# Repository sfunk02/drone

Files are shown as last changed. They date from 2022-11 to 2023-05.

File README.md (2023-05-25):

# Drone

## by Sam Funk and Paul Schakel

#### [Drone 1.0](https://github.com/sfunk02/drone#drone-10) | [Drone 2.0](https://github.com/sfunk02/drone#drone-20) | [Drone 3.0](https://github.com/sfunk02/drone#drone-30) | [Drone 4.0](https://github.com/sfunk02/drone#drone-40) | [Final Takeaways](https://github.com/sfunk02/drone#final-takeaways)

## Introduction

The goal of this project was to create a drone using a Raspberry Pi Pico. The assignment criteria are as follows:
* Survivability: the payload (RPi Pico, sensors, etc) must survive and function post-flight.
* Custom circuit board: breadboards are for prototyping, not for finished products.  Solder headers onto your board so everything is compact but you can add/remove the Pico and other sensors.
* Data collection: your payload must collect data throughout the flight and save that data to the Pico’s onboard storage. Examples: spin rate (MPU6050), altitude (MPL3115A2), location (GPS).
* Data presentation: Show off that data you collected! Plot the data in some way that is meaningful to your project. 

We decided that a drone would be a reasonably challenging way to accomplish this task.

### Project [Planning](docs/Planning.md)

The initial design was derived from a DJI Tello drone. We wanted the drone to be as compact and small as possible to reduce weight so it could be lifted by our Tello motors. We intend to add cages for the propellers to add a level of safety to the drone, but they were not included in our first prototype. The nature of the project is to make something fly with a Raspberry Pi Pico, so that is the microcontroller we chose to use. We decided to power our prototype with a 2000mAh LiPo battery and two DRV8833 H-bridges because we have a surplus of both in our engineering lab.

### Tools Used

* CAD - [Onshape](https://www.onshape.com/en/)
* Code - [VS Code](https://code.visualstudio.com/)
* Wiring Diagram - [Fritzing](https://fritzing.org/)

### Code Prototypes

To make sure we didn't get ahead of ourselves, we created prototypes of the separate parts of the project so that we could test the components before assembling the whole drone:

* [MPU6050 (accelerometer)](/code/prototypes/accelerometer.py)
* [DRV8833 (old H-bridge)](/code/prototypes/drv8833.py)
* [TB6612FNG (new H-bridge)](/code/prototypes/tb6612fng.py)

<br>
<br>

## Drone 1.0

### Bill of Materials

* Raspberry Pi Pico
* 2000mAh LiPo battery
* x2 DRV8833 (old H-bridge)
* MPU6050 (accelerometer)
* PowerBoost
* acrylic
* ABS (3D print material)
* x4 Tello motors
* x4 Tello propellers
* x4 1.25mm female JST connectors
* circuit board
* wires and solder
* hardware to attach arms and base

### CAD [(Onshape)](https://cvilleschools.onshape.com/documents/ce9d8d739d2d9f15e9173bc0/w/6c76af61bf90a62108bdc466/e/912e9d444323990bdd98e468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)

#### Arm
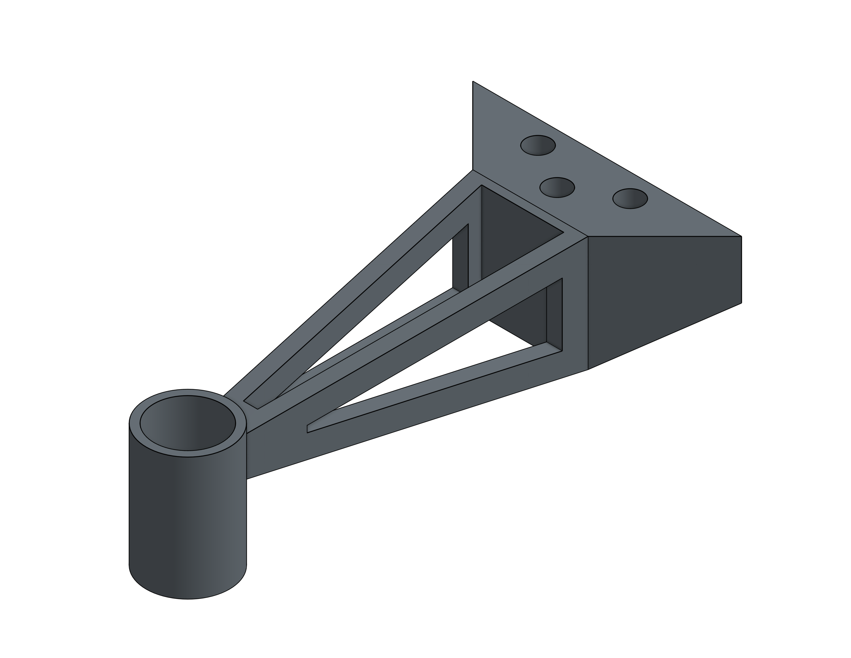
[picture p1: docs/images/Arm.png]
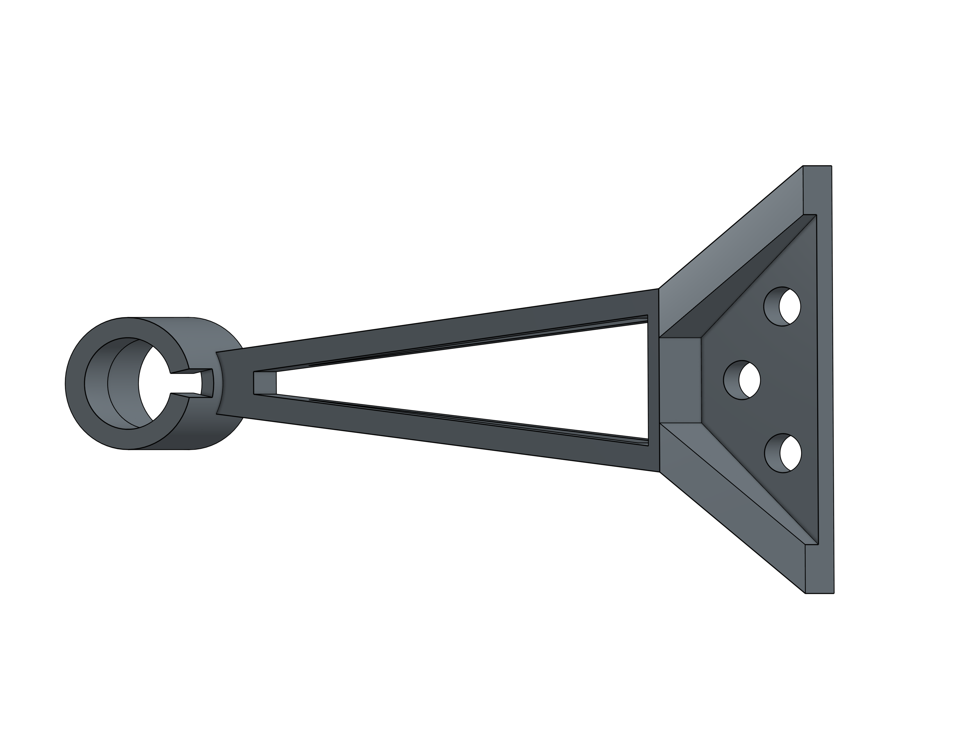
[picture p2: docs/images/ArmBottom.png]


The arm is designed to be lightweight and stable. It accomplishes this with a tapered, hollowed out design. It has a cylinder on the end to fit the motor which acts secondarily as a foot with a small cut-out for wiring to fit through.

#### Base
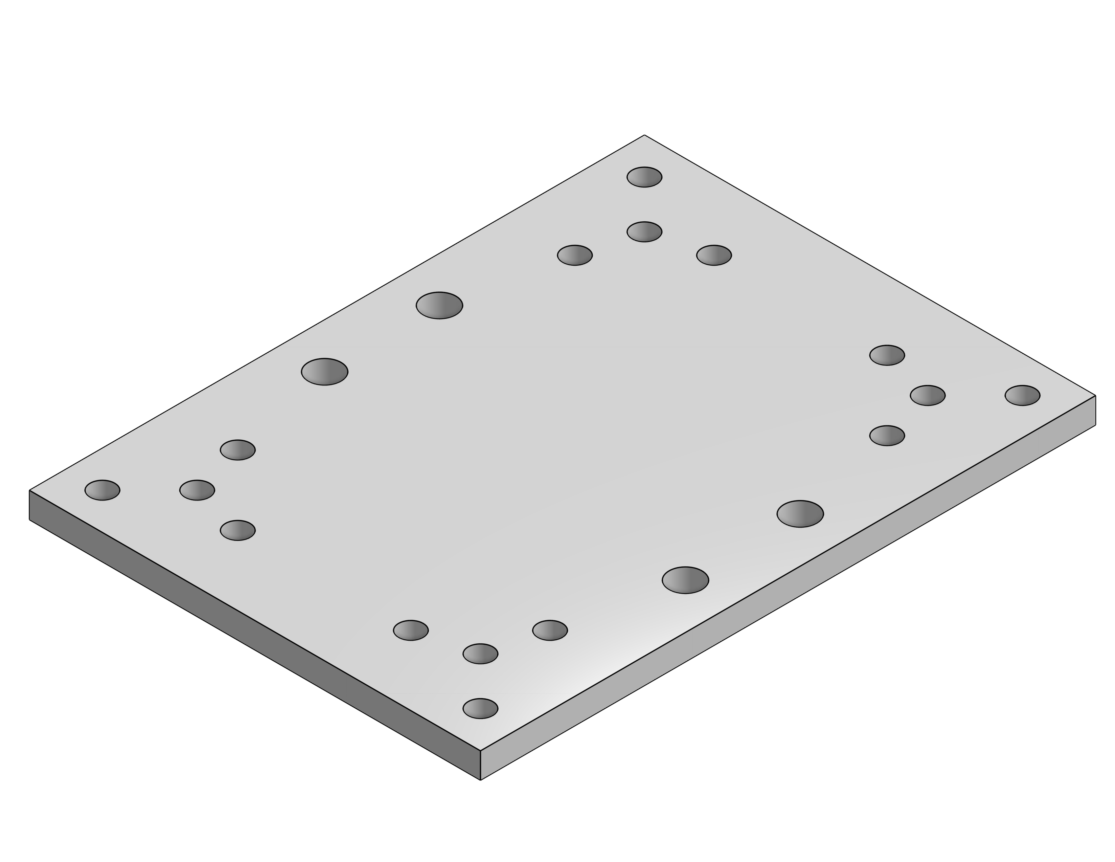
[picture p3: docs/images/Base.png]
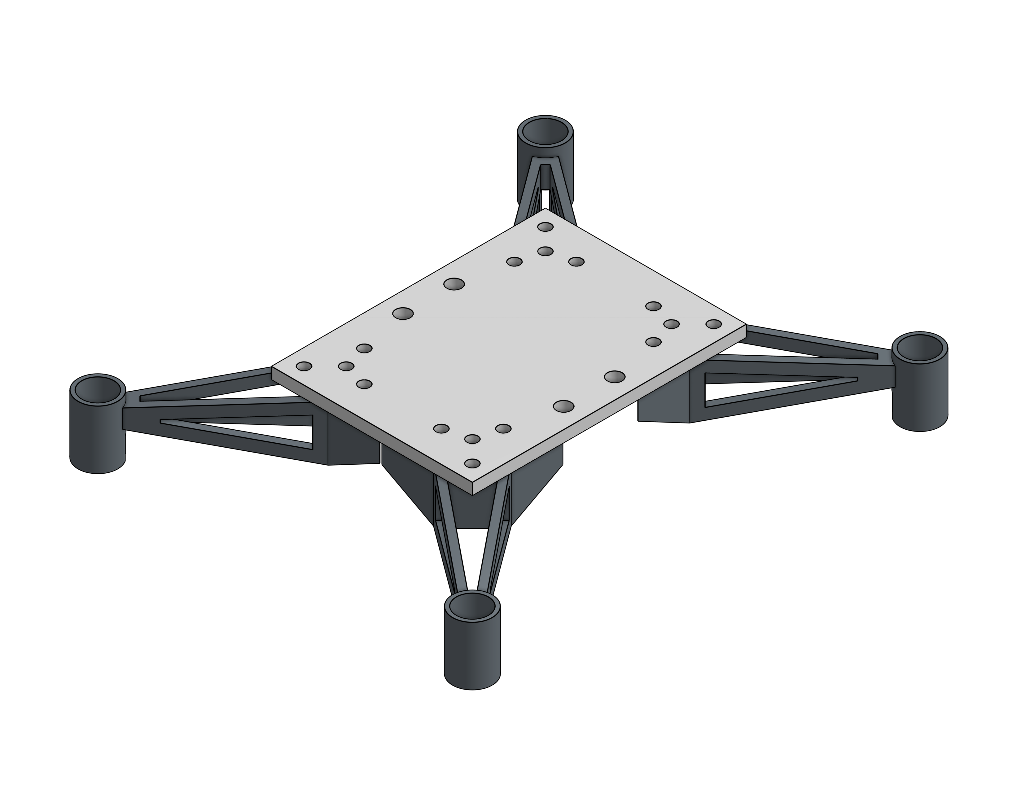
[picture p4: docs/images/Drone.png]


The base is sized to fit our circuit board of components, which includes a Raspberry Pi Pico, two motor h-bridges, an accelerometer/gyro, and a PowerBoost. The CAD assembly allowed me to measure between the arms and make sure there was space to fit the LiPo battery underneath. The four holes in the middle of the base allow the battery to be tied to the drone.

### Code

[Link to Code](code/final_code_1.0.py)

### Wiring

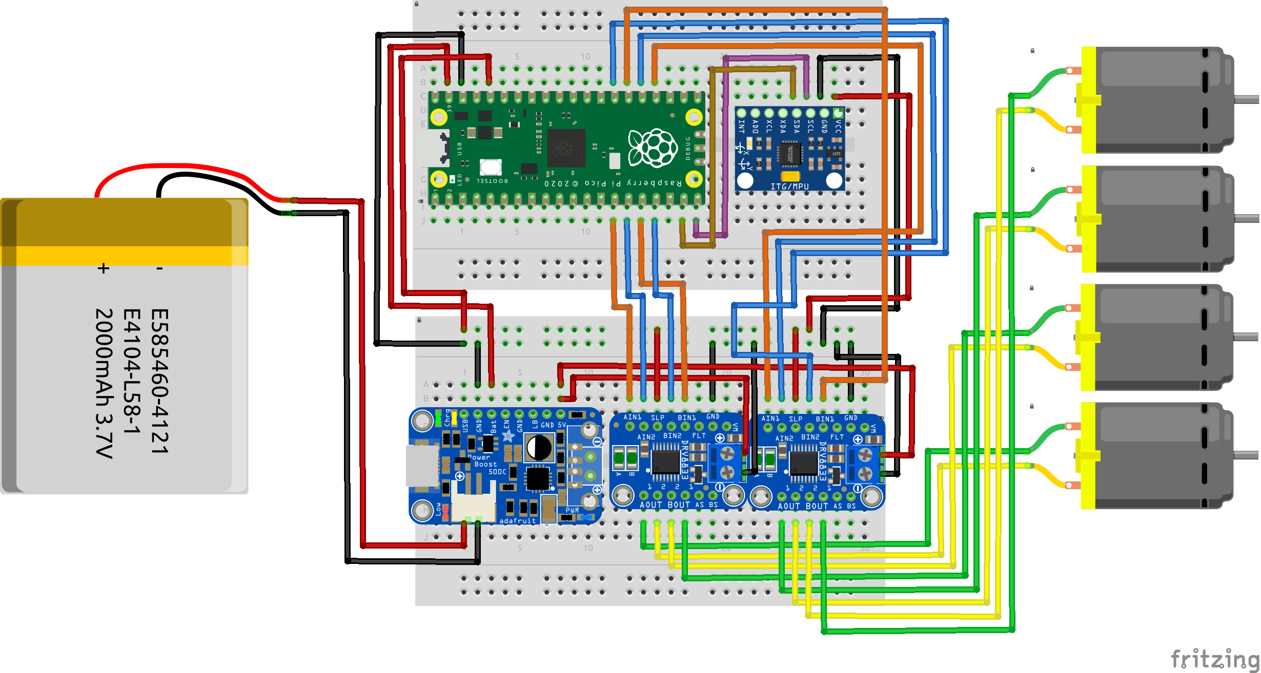
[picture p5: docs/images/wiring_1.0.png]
Drone1Wiring


### Images

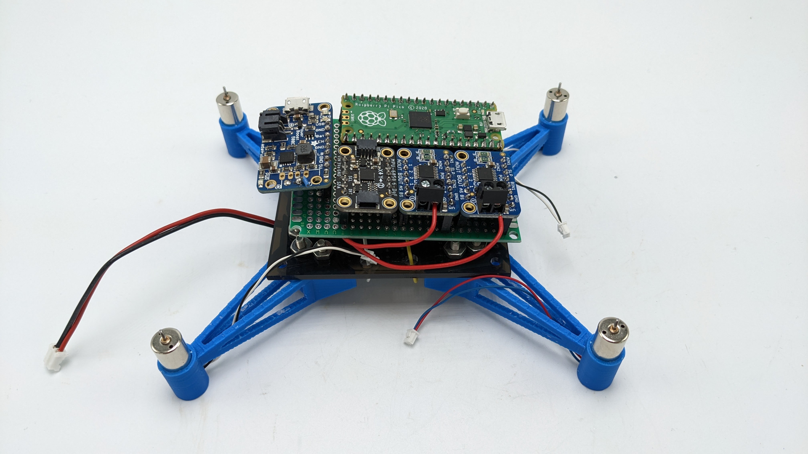
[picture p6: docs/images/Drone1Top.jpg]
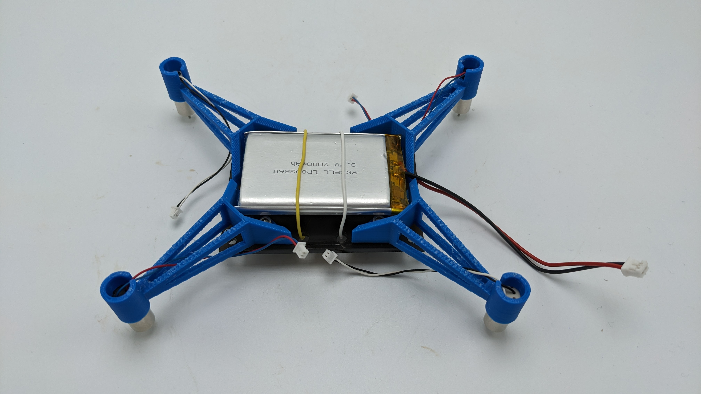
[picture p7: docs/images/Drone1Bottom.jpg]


### Issues

Between the sheet of acrylic, large battery, and unnecessary amount of hardware, our first design was too heavy. We used Tello motors, but our drone weighed almost twice as much as a Tello. We also noticed that our motors were not spinning fast enough when powered through our drone. After a lot of troubleshooting and testing, we determined that this was due to a combination of our battery, PowerBoost, and H-bridges. Both the PowerBoost and the H-bridges were limiting current, and the battery itself couldn't output current fast enough with everything else bypassed.

<br>
<br>

## Drone 2.0

### Bill of Materials

* Raspberry Pi Pico
* 1100mAh Tello battery
* x2 TB6612FNG (new H-bridge)
* MPU6050 (accelerometer)
* ABS (3D print material)
* x4 Tello motors
* x4 Tello propellers
* x4 1.25mm female JST connectors
* circuit board
* wires and solder
* hardware to attach frame to circuit board

Changes:

We switched out our H-bridges and battery, eliminated the PowerBoost, and wired the power source directly to the board to bypass any current limiting. No acrylic was needed because the new design fit the circuit board directly to the ABS frame. We used less hardware because the arms didn't need to be attached separately (see images below).

### CAD [(Onshape)](https://cvilleschools.onshape.com/documents/ce9d8d739d2d9f15e9173bc0/w/6c76af61bf90a62108bdc466/e/912e9d444323990bdd98e468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)

#### Frame
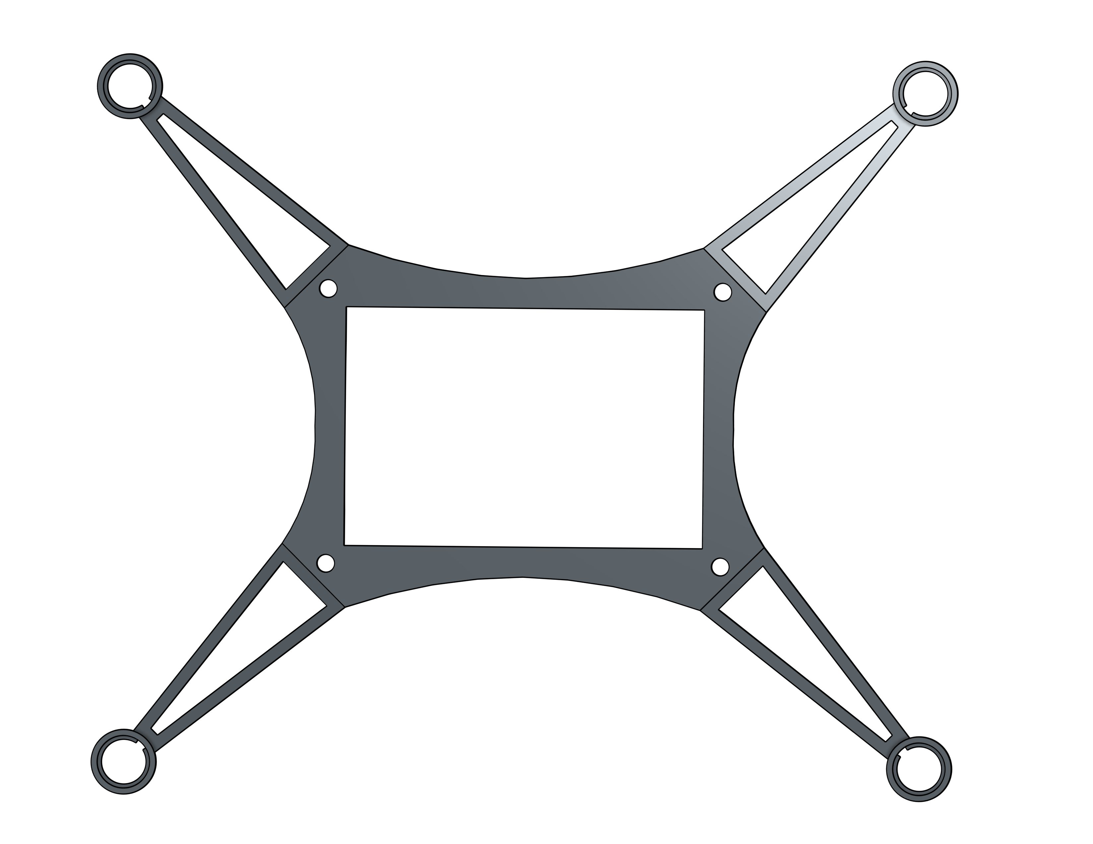
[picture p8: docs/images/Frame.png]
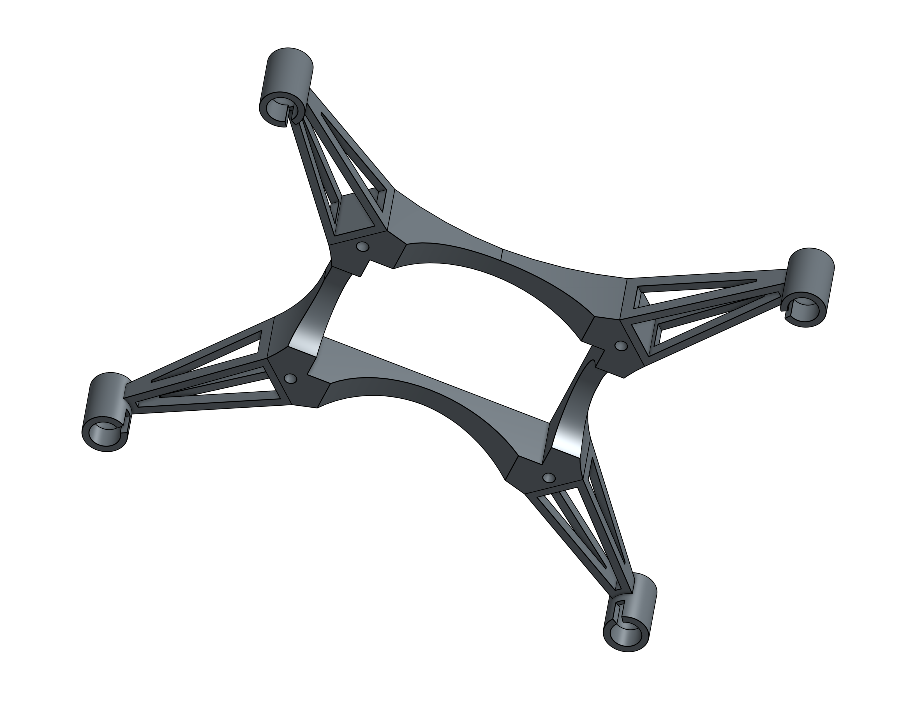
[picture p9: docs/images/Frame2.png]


The new frame design...

### Code

[Link to Code](code/final_code_2.0.py)

### Wiring

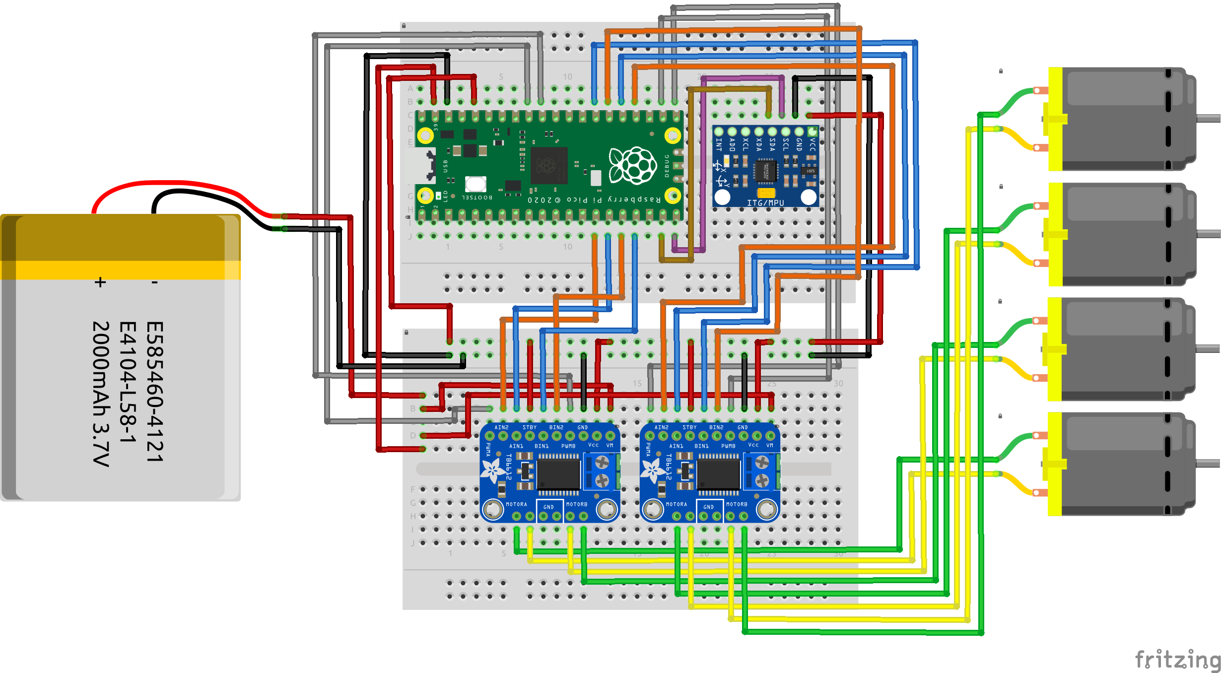
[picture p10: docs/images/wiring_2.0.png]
Drone2Wiring


### Images

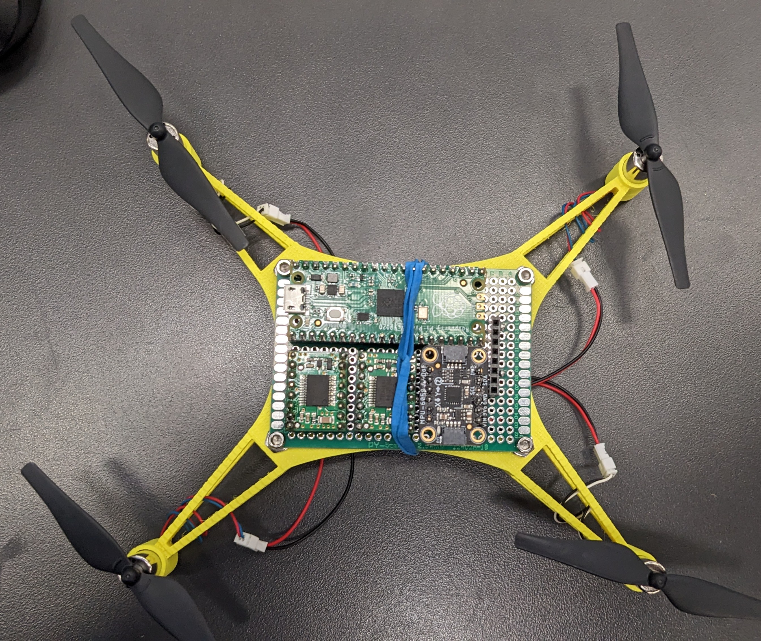
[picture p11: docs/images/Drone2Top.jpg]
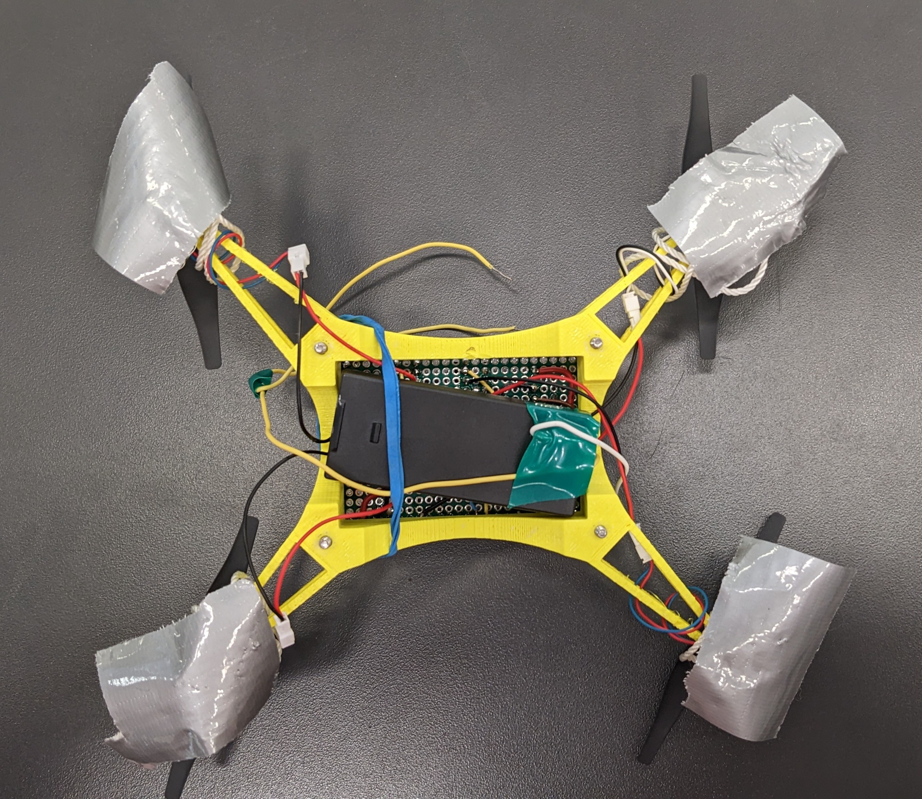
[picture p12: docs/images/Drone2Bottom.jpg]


### Issues

Standby pin disconnected on one h-bridge, PWM signal and 3.3V sent to wrong pins requiring some re-soldering

<br>
<br>

## Drone 3.0

### Bill of Materials

* Raspberry Pi Pico
* 1100mAh Tello battery
* x4 IRLB8721 MOSFETs
* LSM6DSO (accelerometer)
* ABS (3D print material)
* x4 Tello motors
* x4 Tello propellers
* x4 1.25mm female JST connectors
* circuit board
* wires and solder
* hardware to attach frame to circuit board

Changes:

We originally switched out our 2 H-bridges with 4 transistors (1 per motor) and tested it on a breadboard. We found that the amount of current pulled by our motors was too great, and caused the transistors to smoke. To allow a greater flow of current without limiting our voltage, we switched out the transistors with N-Channel MOSFETs that are rated to a much higher current and voltage. They also have heatsinks, and shouldn't overheat like our previous H-bridges. We also switched out our MPU6050 accelerometer for a more accurate LSM6DSO.

### Code

[Link to Code](code/final_code_3.0.py)

### Wiring

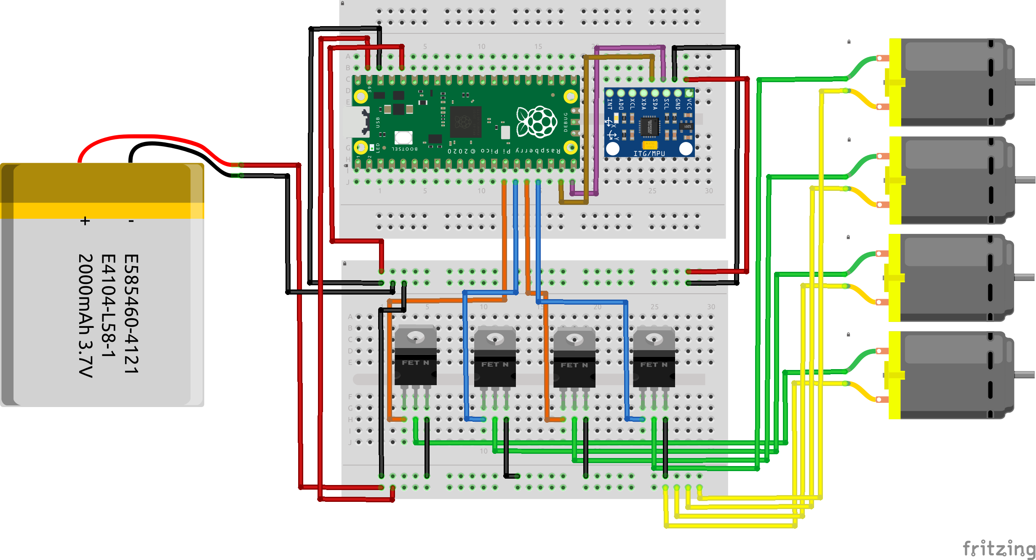
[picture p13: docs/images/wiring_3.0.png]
Drone3Wiring


### Images

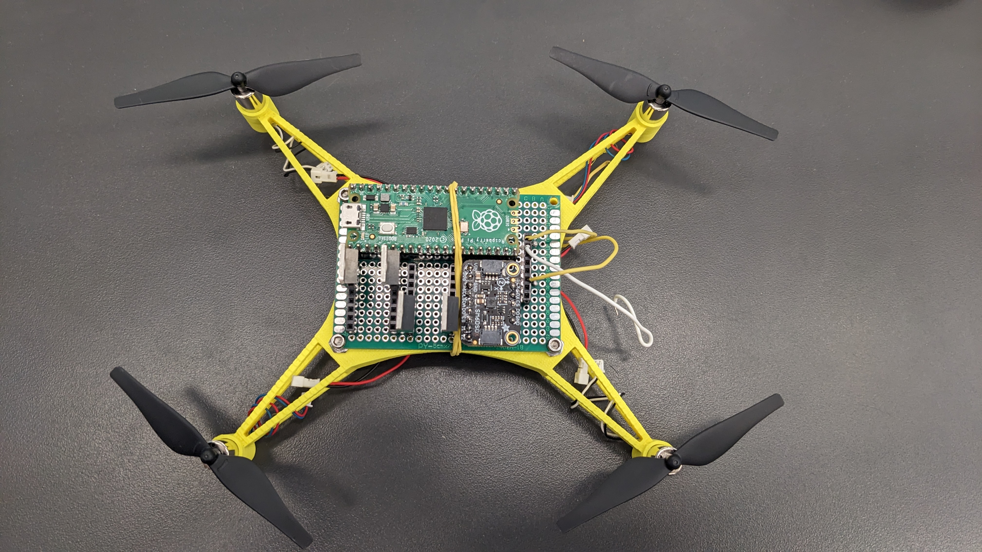
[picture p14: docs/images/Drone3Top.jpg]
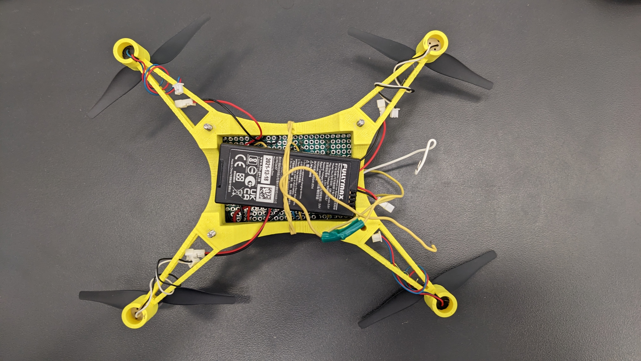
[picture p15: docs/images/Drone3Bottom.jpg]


### Issues

The Pico keeps wiping at seemingly random times, leading us to believe that there is a short somewhere in the circuitry caused by continual movement of the drone. We aren't able to trace the short and decided it would be better to solder a new circuit board. Additionally, the rectangular shape of the drone causes issues with the code for the accelerometer, and the battery is only attached with a rubber band. Drone 4.0 will address all of these problems.

<br>
<br>

## Drone 4.0

### Bill of Materials

* Raspberry Pi Pico
* 1100mAh Tello battery
* x4 IRLB8721 MOSFETs
* LSM6DSO (accelerometer)
* ABS (3D print material)
* x4 Tello motors
* x4 Tello propellers
* x4 1.25mm female JST connectors
* circuit board
* wires and solder
* hardware to attach frame to circuit board

Changes:

We soldered a new circuit board and redesigned/printed a new frame for the drone. The new circuit board has cleaner soldering to reduce the risk of shorts and includes a power switch for easier usage. The new frame is square in shape to make the accelerometer readings more accurate in relation to the motor positions and also has a built in mount for the battery.

### CAD [(Onshape)](https://cvilleschools.onshape.com/documents/ce9d8d739d2d9f15e9173bc0/w/6c76af61bf90a62108bdc466/e/912e9d444323990bdd98e468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)

#### Frame (updated)
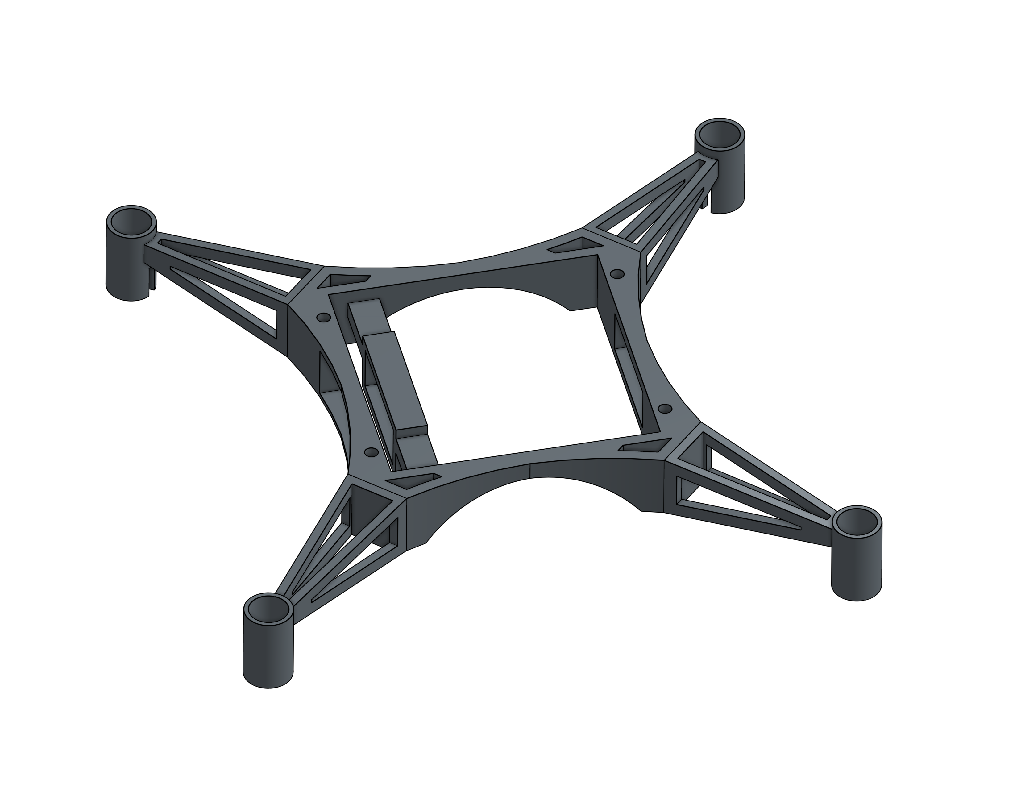
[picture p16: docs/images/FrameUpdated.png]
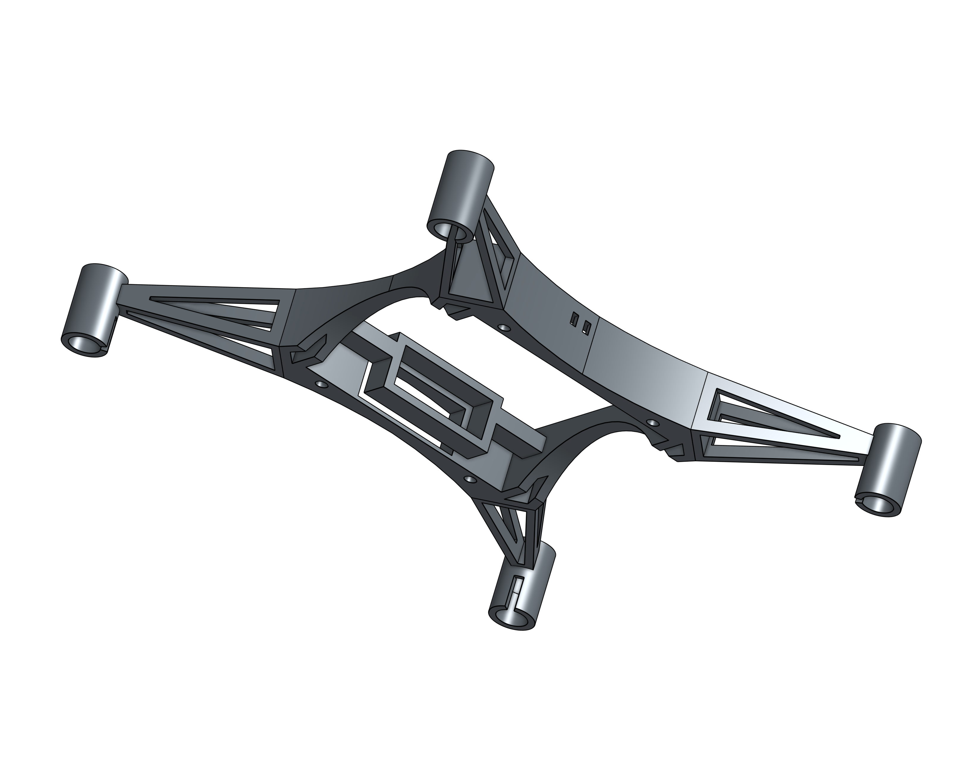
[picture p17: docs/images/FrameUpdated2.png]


The square frame design is intended to result in better stability and a more accurate PID function. The updated design also includes a mount for the battery.

### Code

[Link to Code](code/final_code_4.0.py)

### Wiring

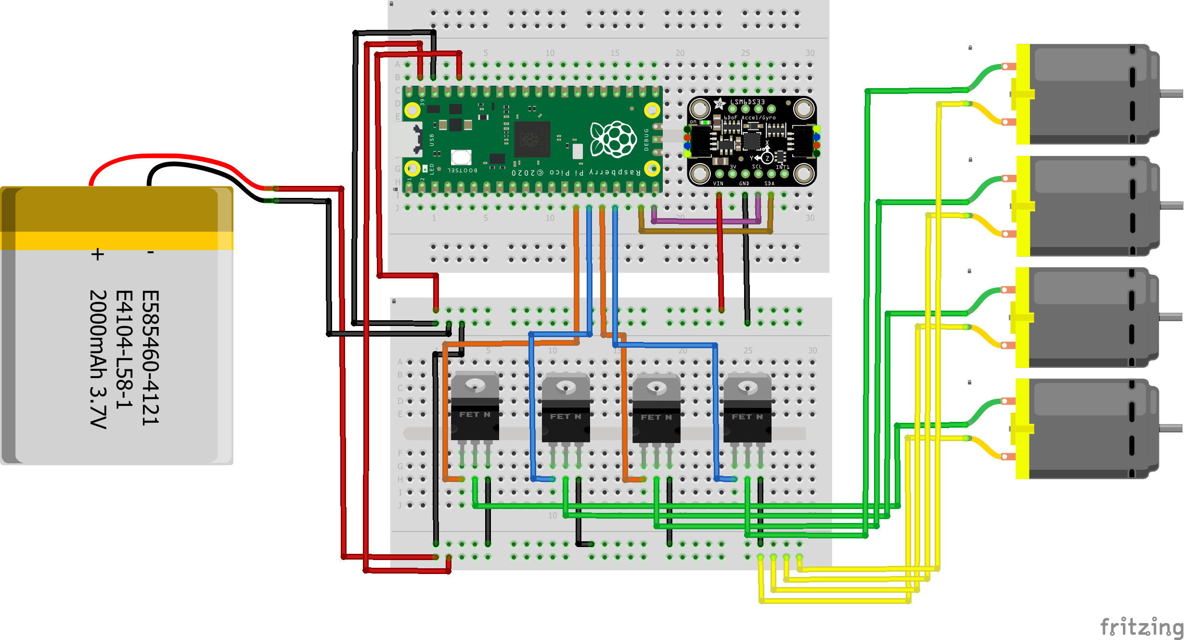
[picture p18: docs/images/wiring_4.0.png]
Drone4Wiring


### Images

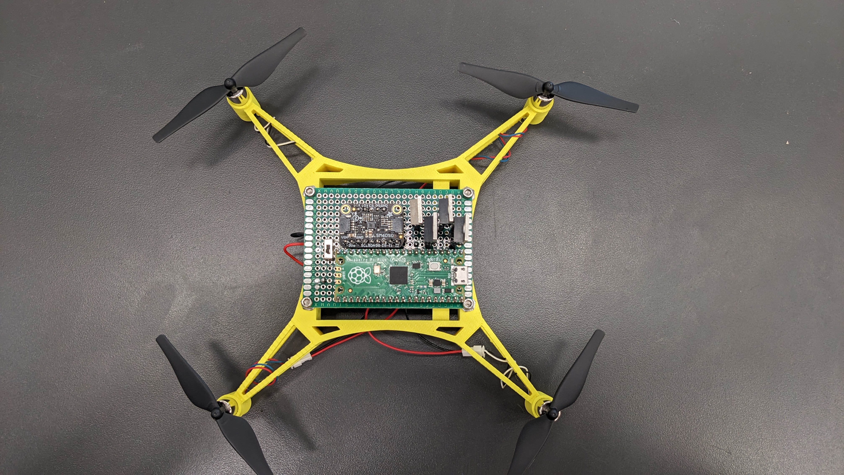
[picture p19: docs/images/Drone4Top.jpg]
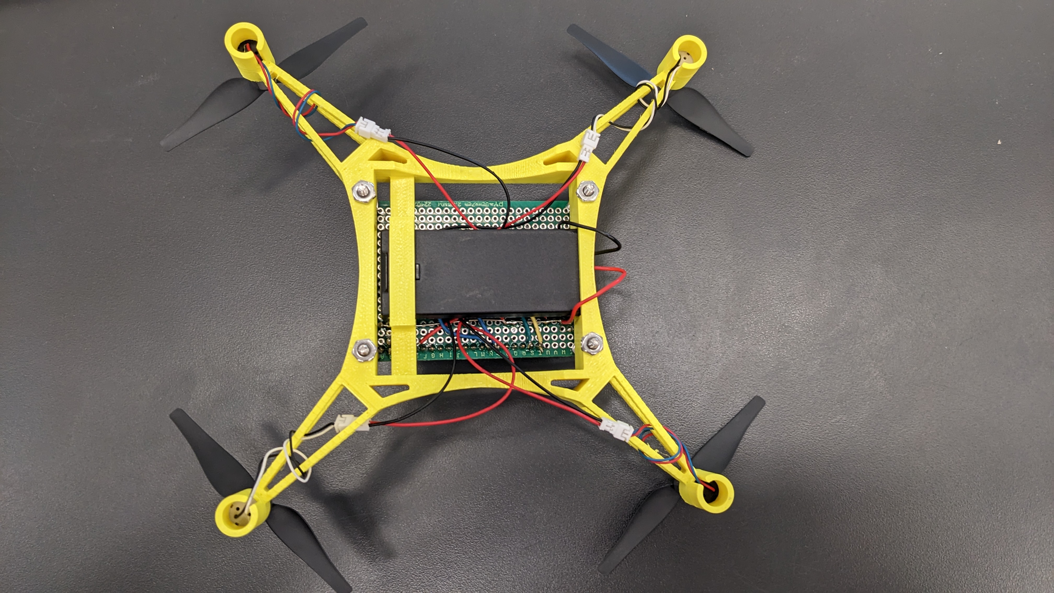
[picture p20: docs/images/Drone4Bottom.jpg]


### Issues

The power switch melted because we sent more current through it than it could handle. We replaced it with a much heavier duty panel-mount style switch. Then, the wires going to the battery started melting so we replaced them with much heavier gauge wire. To add data logging functionality, we had to add another small switch to the circuit board to switch the Pi between read-only mode and write-only mode.

<br>
<br>

## Final Takeaways

### Test Bench:

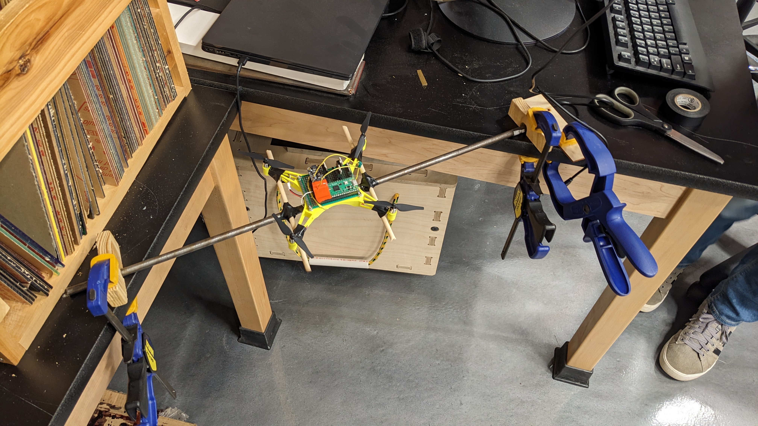
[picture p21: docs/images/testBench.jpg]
testBench


The test bench was the system we developed to code and tune our PID for the drone. Our original setup was a board with the drone attached by strings. This didn't work very well, as the drone would swing back and forth on the strings and was never able to balance itself in the middle. We instead opted to have a rod to which the drone was attached, which moved the fulcrum point directly to the bottom of the drone. We still had trouble with getting it to balance, but our PID did seem to get a bit better than it had previously been.

### Final Launch:



Unfortunately, our drone did not work very well. We think that the PID caused the drone to launch sideways instead of up, which is why it went straight into the ground. If we had more time to tune the PID, we probably could've gotten it to hover and balance itself. We also maybe could've had a more successful launch if we disabled PID altogether, but that would've been sad because we spent multiple weeks on it.

### Graph of Data:

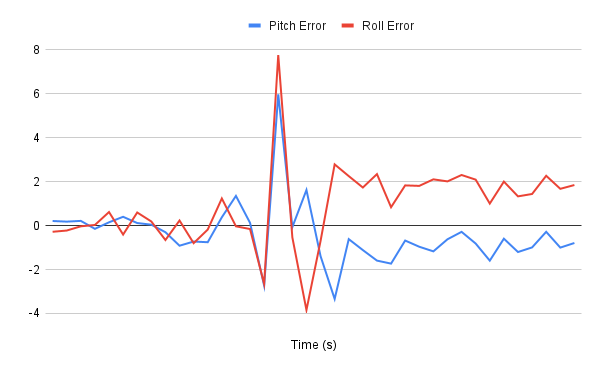
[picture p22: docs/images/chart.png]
chart


As you can see in the graph, there is a large spike in both pitch and roll error in the middle, followed by a drop and an approximate flatline. The spike is when the drone lurches sideways off the cone, causing a lot of force to act on the accelerometer. The drop is when the drone hits the ground, and then the flatline follows when it stays in the same place for a few seconds.

### Final Reflection:

We learned a lot about code, PID, and 3D design throughout the duration of this project. Unfortunately, we never got it working 100%, but we did get very close. Designing a drone was a very fun challenge and I'm glad we attempted it. If we had more time, we potentially would have been able to properly tune the PID and get the drone to balance itself. We also wanted to add an additional board to the drone that would allow it to connect to a controller and be maneuvered wirelessly during flight. Even though we didn't get it working, I am now confident in my ability to design and create a new drone in only 2-3 class periods.

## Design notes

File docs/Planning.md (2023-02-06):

## Drone
### By Paul Schakel and Sam Funk

### Project Vision
Drone to lift a raspberry pi pico off the ground because the fact that it is on the ground is a problem. A drone seems like the all around simplest solution to this problem.
Success = working drone
Risk mitigation: cages around propellers, only flight test with teacher supervision, safety glasses

&nbsp;

### Drawing
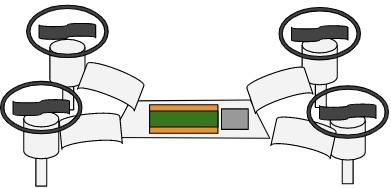
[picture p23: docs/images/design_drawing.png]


Central platform will hold Pico, circuit board, and battery. Four arms will extend out to hold the motors + propellers, which will have a guard/cage around them and a leg/foot underneath. 

&nbsp;

### Code 
Need to: 
* Connect to controller
* Initiate motors
* Collect accelerometer data

While true:
* Check for input from controller - > move based on input
* Constant balancing - make force of propellers equal to force of gravity

Need several functions - rotate, move up and down, tilt
* Move up - force of propellers greater than force of gravity - higher motor speed
* Move down - force of propellers less than force of gravity - lower motor speed
* Tilt - allows to move laterally - two motors at higher speed than others
* Rotation - two types of propellers used to cancel out torque - 1 and 3 are one type, 2 and 4 are another. These two types rotate in different directions to cancel out torque. To rotate the drone, one of the types of propellers have to spin at a higher speed than the other

&nbsp;

### What We Need to Learn
* Wireless connection (bluetooth?)
* Wireless remote/controller
* PID

&nbsp;

### Bill of Materials
* Acrylic (~4 sq. feet)
* 3D print material maybe
* Propellers (4)
* LiPo battery (1)
* Raspberry pi pico (1)
* Altimeter (1)
* Accelerometer (1)
* Hardware - nuts and bolts, maybe standoffs for Pico

&nbsp;

### Schedule
11/28 - finish planning, research motors, aerodynamics, etc

12/5 - discuss + order propellers, start working on CAD and code
	Initial wiring for code testing
	
12/12 - CAD - finish main drone body. Code - Start prototyping first flight functions - vertical, horizontal, spinning movement

Winter Break

1/3 - CAD - design brackets + cages for motors and brackets for arms. Code - Start getting motors to work

1/9 - CAD - finalize design, maybe cut/print. Code - PID

1/17 - CAD - Cut/print, assemble drone. Code - PID

1/24 - learn how to make a circuit board and design it. Continue working on PID

1/30 - print circuit board and wire everything. Finish PID

2/6 - See if it works

2/13 - testing, tweaking coding

2/21 - testing and tweaking

2/27 - “Design refinement and final tweaks”

3/6 - add bluetooth

3/13 - add bluetooth

3/20 - add bluetooth

3/27 - test/tweak bluetooth controller

Spring Break

4/10 - Fly drone around

4/17 - fly it some more

4/24 - show off / brag

5/1 - “Analyze data + finalize documentation”

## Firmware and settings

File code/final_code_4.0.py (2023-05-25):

#type: ignore
# Paul Schakel
# Prototype for PID control

import board
import pwmio
from adafruit_lsm6ds.lsm6dso32 import LSM6DSO32
import busio
import time
import math

# Initialize Motors
MOTOR_1 = board.GP11
MOTOR_2 = board.GP21
MOTOR_3 = board.GP10
MOTOR_4 = board.GP20
motor1_pwm = pwmio.PWMOut(MOTOR_1, frequency=1000)
motor2_pwm = pwmio.PWMOut(MOTOR_2, frequency=1000)
motor3_pwm = pwmio.PWMOut(MOTOR_3, frequency=1000)
motor4_pwm = pwmio.PWMOut(MOTOR_4, frequency=1000)

# Initialize accelerometer
sda_pin = board.GP16
scl_pin = board.GP17
i2c = busio.I2C(scl_pin, sda_pin)
sensor = LSM6DSO32(i2c)

# Initialize LED
led = digitalio.DigitalInOut(board.LED)
led.direction = digitalio.Direction.OUTPUT

# Variables for time tracking
last_update = time.monotonic()
start_time = time.monotonic()

# PID values
Kp = 0.23
Ki = 0.1
Kd = 0.0

PID_multiplier = 1000

# Used for changing speed of all motors
motor_baseline = 0

# Variables keeping track of data
error_pitch = 0
error_roll = 0
error_yaw = 0

last_errors_pitch = []
last_errors_roll = []
last_errors_yaw = []

avg_error_pitch = 0
avg_error_roll = 0
avg_error_yaw = 0

last_avg_error_pitch = 0
last_avg_error_roll = 0
last_avg_error_yaw = 0

integral_pitch = 0
integral_roll = 0
integral_yaw = 0

derivative_pitch = 0
derivative_roll = 0
derivative_yaw = 0

setpoint = 0

pitch_PID = 0
roll_PID = 0
yaw_PID = 0

pitch_data = []
roll_data = []

while True:
    x = sensor.acceleration[0]
    y = sensor.acceleration[1]
    if x == 0: # Prevent div by 0 error
        x = 0.000001

    angle = math.degrees(math.atan(y/x))
    intensity = math.sqrt((x**2) + (y**2))

    if intensity > 9.8: # Make sure we dont have extra intensity
        intensity = 9.8

    # Find quadrant and make angle between 0 and 360
    if x < 0 and y > 0: # Q2
        angle += 360
    elif x > 0 and y > 0: # Q3
        angle += 180
    elif x > 0 and y < 0: #Q4
        angle += 180

    now = time.monotonic()
    dt = now - last_update

    angle -= 45 # Change angle to reflect orientation of accelerometer

    if angle > 360:
        angle -= 360

    run_time = now - start_time

    # Ramp the motors up and down for a short time
    if run_time < 2:
        if motor_baseline < 0.7:
            motor_baseline += 0.005
    if run_time > 2 and run_time < 4:
        if motor_baseline > 0.1:
            motor_baseline -= 0.005
    if run_time > 4:
        break
        
    
    error_pitch = setpoint - (intensity * math.cos(math.radians(angle))) # Find error value for pitch
    last_errors_pitch.append(error_pitch) # Used to average error values
    avg_error_pitch = sum(last_errors_pitch) / len(last_errors_pitch) # Take average
    error_roll = setpoint - (intensity * math.sin(math.radians(angle))) # Find error value for roll
    last_errors_roll.append(error_roll) # Used to average error values
    avg_error_roll = sum(last_errors_roll) / len(last_errors_roll) # Take average

    # Find integral value for PID
    integral_pitch = integral_pitch + dt * avg_error_pitch
    integral_roll = integral_roll + dt * avg_error_roll

    # Find derivative value for PID
    derivative_pitch = (avg_error_pitch - last_avg_error_pitch)/dt
    derivative_roll = (avg_error_roll - last_avg_error_roll)/dt

    # Find final PID values
    pitch_PID =  Kp * avg_error_pitch + Ki * integral_pitch + Kd * derivative_pitch
    roll_PID = Kp * avg_error_roll + Ki * integral_roll + Kd * derivative_roll

    PID_scaler = PID_multiplier * intensity # Scale PID so it can control the motors better

    # Determining the motor speeds
    motor1_duty_cycle = int(65535 * motor_baseline - pitch_PID * PID_scaler)
    motor2_duty_cycle = int(65535 * motor_baseline - roll_PID * PID_scaler)
    motor3_duty_cycle = int(65535 * motor_baseline + pitch_PID * PID_scaler)
    motor4_duty_cycle = int(65535 * motor_baseline + roll_PID * PID_scaler)

    # Make sure motor speeds don't exceed limits
    if motor1_duty_cycle > 65535:
        motor1_duty_cycle = 65535
    if motor2_duty_cycle > 65535:
        motor2_duty_cycle = 65535
    if motor3_duty_cycle > 65535:
        motor3_duty_cycle = 65535
    if motor4_duty_cycle > 65535:
        motor4_duty_cycle = 65535
    if motor1_duty_cycle < 2000:
        motor1_duty_cycle = 2000
    if motor2_duty_cycle < 2000:
        motor2_duty_cycle = 2000
    if motor3_duty_cycle < 2000:
        motor3_duty_cycle = 2000
    if motor4_duty_cycle < 2000:
        motor4_duty_cycle = 2000

    print("\nmotor1_pwm.duty_cycle: " + str(motor1_duty_cycle))
    print("motor3_pwm.duty_cycle: " + str(motor3_duty_cycle))
    print("motor2_pwm.duty_cycle: " + str(motor2_duty_cycle))
    print("motor4_pwm.duty_cycle: " + str(motor4_duty_cycle))
    print("motor_baseline: " + str(motor_baseline))
    print("pitch_PID: " + str(pitch_PID))

    # Setting the motor speeds
    motor1_pwm.duty_cycle = motor1_duty_cycle
    motor2_pwm.duty_cycle = motor2_duty_cycle
    motor3_pwm.duty_cycle = motor3_duty_cycle
    motor4_pwm.duty_cycle = motor4_duty_cycle

    # Update timer
    last_update = now

    # Save last error values for derivative calculation
    last_avg_error_pitch = avg_error_pitch
    last_avg_error_roll = avg_error_roll

    # Update error averaging values
    if len(last_errors_pitch) > 5:
        last_errors_pitch.pop(0)
    if len(last_errors_roll) > 5:
        last_errors_roll.pop(0)

    # Save data for saving to filesystem when flight is done
    pitch_data.append(error_pitch)
    roll_data.append(error_roll)

# Turn motors off when the flight is done
motor1_pwm.duty_cycle = 0
motor2_pwm.duty_cycle = 0
motor3_pwm.duty_cycle = 0
motor4_pwm.duty_cycle = 0

led.value = True # Turn LED on while saving data

with open("/error.txt", "a") as datalog:
    datalog.write('Pitch_Error,Roll_Error\n')  # Title for the log file
    datalog.flush()
    for i in range(0, len(pitch_data), 10):
        datalog.write('{},{}\n'.format(pitch_data[i], roll_data[i]))  # Storing error data on the log file
        datalog.flush()

led.value = False # Turn LED off
time.sleep(2)

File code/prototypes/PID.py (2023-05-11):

# Paul Schakel
# Prototype for PID control

import board
import pwmio
from adafruit_lsm6ds.lsm6dso32 import LSM6DSO32
import busio
import time
import math

MOTOR_1 = board.GP20
MOTOR_2 = board.GP21
MOTOR_3 = board.GP10
MOTOR_4 = board.GP11
motor1_pwm = pwmio.PWMOut(MOTOR_1, frequency=1000)
motor2_pwm = pwmio.PWMOut(MOTOR_2, frequency=1000)
motor3_pwm = pwmio.PWMOut(MOTOR_3, frequency=1000)
motor4_pwm = pwmio.PWMOut(MOTOR_4, frequency=1000)

sda_pin = board.GP16
scl_pin = board.GP17
i2c = busio.I2C(scl_pin, sda_pin)

sensor = LSM6DSO32(i2c)

last_update = time.monotonic()

Kp = 0.3
Ki = 0.05
Kd = 0.3

motor1_baseline = .7
motor2_baseline = .7
motor3_baseline = .7
motor4_baseline = .7

PID_multiplier = 800

error_pitch = 0
error_roll = 0
error_yaw = 0

last_error_pitch = 0
last_error_roll = 0
last_error_yaw = 0

integral_pitch = 0
integral_roll = 0
integral_yaw = 0

derivative_pitch = 0
derivative_roll = 0
derivative_yaw = 0

throttle = 0

pitch_force = 0

setpoint = 0

pitch_PID = 0
roll_PID = 0
yaw_PID = 0

while True:
    x = sensor.acceleration[0]
    y = sensor.acceleration[1]
    if x == 0:
        x = 0.000001
    angle = math.degrees(math.atan(y/x))
    intensity = math.sqrt((x**2) + (y**2))

    if intensity > 9.8:
        intensity = 9.8

    # Find quadrant and make angle between 0 and 360
    if x < 0 and y > 0: # Q2
        angle += 360
    elif x > 0 and y > 0: # Q3
        angle += 180
    elif x > 0 and y < 0: #Q4
        angle += 180

    now = time.monotonic()
    dt = now - last_update

    angle += 45

    if angle > 360:
        angle -= 360

    error_pitch = setpoint - (intensity * math.cos(math.radians(angle)))
    error_roll = setpoint - (intensity * math.sin(math.radians(angle)))

    integral_pitch = integral_pitch + dt * error_pitch
    integral_roll = integral_roll + dt * error_roll

    derivative_pitch = (error_pitch - last_error_pitch)/dt
    derivative_roll = (error_roll - last_error_roll)/dt

    pitch_PID =  Kp * error_pitch + Ki * integral_pitch + Kd * derivative_pitch
    roll_PID = Kp * error_roll + Ki * integral_roll + Kd * derivative_roll

    PID_scaler = PID_multiplier * intensity

    motor1_duty_cycle = int(65535 * motor1_baseline - pitch_PID * PID_scaler)
    motor2_duty_cycle = int(65535 * motor2_baseline - roll_PID * PID_scaler)
    motor3_duty_cycle = int(65535 * motor3_baseline + pitch_PID * PID_scaler)
    motor4_duty_cycle = int(65535 * motor4_baseline + roll_PID * PID_scaler)

    if motor1_duty_cycle > 65535:
        motor1_duty_cycle = 65535
    if motor2_duty_cycle > 65535:
        motor2_duty_cycle = 65535
    if motor3_duty_cycle > 65535:
        motor3_duty_cycle = 65535
    if motor4_duty_cycle > 65535:
        motor4_duty_cycle = 65535
    if motor1_duty_cycle < 2000:
        motor1_duty_cycle = 2000
    if motor2_duty_cycle < 2000:
        motor2_duty_cycle = 2000
    if motor3_duty_cycle < 2000:
        motor3_duty_cycle = 2000
    if motor4_duty_cycle < 2000:
        motor4_duty_cycle = 2000


    print("\nmotor1_pwm.duty_cycle: " + str(motor1_duty_cycle))
    print("motor3_pwm.duty_cycle: " + str(motor3_duty_cycle))

    motor1_pwm.duty_cycle = motor1_duty_cycle
    motor2_pwm.duty_cycle = motor2_duty_cycle
    motor3_pwm.duty_cycle = motor3_duty_cycle
    motor4_pwm.duty_cycle = motor4_duty_cycle
    last_error_pitch = error_pitch
    last_error_roll = error_roll
    last_update = now

    time.sleep(.07)

    #print("\nangle: " + str(angle))
    #print("pitch_PID: " + str(pitch_PID))
    #print("integral_pitch: " + str(integral_pitch))
    #print("derivative_pitch: " + str(derivative_pitch))
    #print("error_pitch: " + str(error_pitch))

    #temp_baseline = float(input("Enter baseline: "))
    #motor1_baseline = temp_baseline
    #motor2_baseline = temp_baseline
    #motor3_baseline = temp_baseline
    #motor4_baseline = temp_baseline

    #print(f"x: {round(sensor.acceleration[0], 3)} y: {round(sensor.acceleration[1], 3)} z: {round(sensor.acceleration[2], 3)}")

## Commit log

2022-12-05 Create initial prototype for motor control
2023-02-06 Initial prototype of motor functionality
2023-02-06 Add 2 non-functional prototypes
2023-02-06 Finish prototype of new motor control
2023-02-07 Create first version of wiring diagram
    [wiring_v1.fzz]
2023-02-07 Add ToC and more of a framework for the documentation to be built around
2023-02-08 Add prototype for accelerometer
2023-02-08 Rename prototype for DRV8833
2023-02-08 Finish prototype of TB6612FNG
2023-02-08 Move final code outside prototypes folder and redo it for new h-bridges
2023-02-08 Start working on Code Prototype documentation
2023-02-09 Add wiring image to documentation
2023-02-23 Add wiring for drone 2.0
    [wiring_v2.fzz]
2023-02-23 Add wiring for drone 3.0
    [wiring_v3.fzz]
2023-02-23 Add wiring and code links to README
2023-02-23 Add a couple prototypes
2023-02-23 Add initial PID code
2023-02-23 Change motor pins for drone 3.0
2023-02-24 Start working on PID code
2023-02-27 Make some little changes to the PID prototype
2023-02-27 Start working on converting accelerometer values to angles
2023-03-01 Begin work on finding error, integral, derivative for pitch and roll
    [PID.py]
2023-03-02 Work on PID
2023-03-08 Get better accelerometer working
2023-03-08 Add new accelerometer to PID
2023-03-10 Continue working on PID tuning
2023-03-15 More work on PID
2023-03-22 PID Tuning changes
2023-03-30 Continue working on PID
2023-05-25 Fix a couple typos
2023-05-25 Finish wiring
    [wiring_v4.fzz]
